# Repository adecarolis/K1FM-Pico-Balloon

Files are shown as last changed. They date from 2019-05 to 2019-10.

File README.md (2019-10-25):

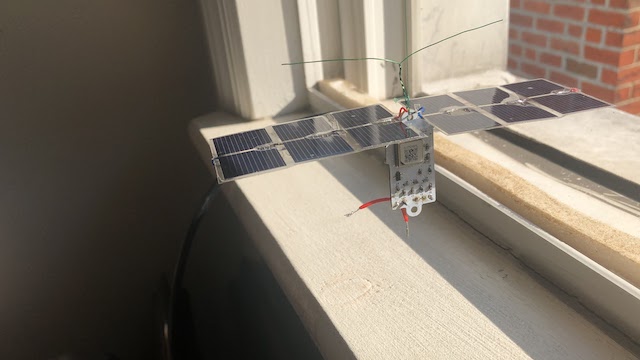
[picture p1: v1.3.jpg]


# K1FM Pico Balloon

## Introduction:

This tracker board is WSPR based and transmits on 20 meters. Version 1.3 weights 2.84 grams and takes around 55mA at 3.3V. Unlike other designs, this one includes a passband filter that significantly smooths the resulting waveforms (such filter would be legally mandatory in the United States). The board includes a power regulator and a low voltage dropout diode that can be useful if using batteries.

A maiden flight, powered by 6 39x19mm Aoshike solar panels, was attempted in New Jersey at the end of September 2019. After 5 days of transmissios the payload failed somewhere around Belize (central America) probably after encountering a tropical storm.

The recommended software is [GeminiWSPR](https://github.com/adecarolis/GeminiWspr)

Feel free to test these boards. You can purchase the latest revision (1.3) at OSHPark:

https://oshpark.com/shared_projects/ud3vH8MF

Suggestions and technical advice are welcome!

73 de Alain K1FM

## Assembly:

This is the recommended assemply sequence. Test each step individually. Do not proceed furter in case you enconter a problem in the current step.

- Install U1, C2, C3, C12, J2, Y1, R1, R2, R5 (Microcontroller)
- Use a USBasp programmer to load the Arduino bootloader (Atmel328p, 8MHz) via the ICSP port. Verify the bootloader can be uploaded without errors.
- Disconnect the USBasp from the J2 port. Connect a serial Arduino programmer to J3 (use 3V and GND connections from J2). Load the GeminiWSPR firmware (don't forget to set your own callsign and gridsquare!). Verify debug output can be seen on the serial monitor.
- Install GPS1, R6, Q2, C10 (GPS)
- Connect the GPS antenna
- In the Arduino serial monitor, verify the GPS is working
- Install Q1, U2, C11, C13, C14, R3, R4, R8, Q3 (Transmitter)
- Install L1, L2, L3, C5, C6, C7, C8, C9 (Bandpass filter)
- Connect the HF antenna 
- Verify the unit transmits WSPR on 14.0956 MHz
- Install U3, C1, C4, D1 (Power Supply)
Note: this is not needed if your power source is externally regulated or never exceeds 3.5 Volts
- Disconnect all J3/J2 connections. Verify the unit can be normally powered via J4

## Changelog:

**Version 1.0**
Initial, not functioning prototype.

**Version 1.1**
- Bugfixes

**Version 1.2**
- Added optional K1FM Pico Power board for battery charge management
- Added bottom hook for dipole antennas
- Replaced Si5351a quartz with TCXO (Q1)
- Added switches to power the Si5351a, GPS down (Q2 - Q3)
- Added temperature sensor (TMP-36)
- Added fixed V_BCK connection to 3.3V
- Added VDD measurement point (ADC0)

**Version 1.3**
- Switched to 4 Layers design
- Added Time Pulse feedback to external interrupt input (PD2)
- Added Clock Generator Feedback to T1 input (PD5)
- Added external SDA, SCL pins
- Added extra power pin for direct battery charging via Schottky diode
- Reorganized external pins, added standard ISCP header
- 4.7 voltage divider on ADC0
- Fixed Q2-Q3 Mosfet polarization
- Expanded gap between main board and "Remove Before Flight" section

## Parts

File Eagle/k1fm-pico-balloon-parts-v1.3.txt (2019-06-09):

Partlist

Exported from k1fm-pico-balloon-v1.3.brd at 6/9/19 8:12 AM

EAGLE Version 9.4.1 Copyright (c) 1988-2019 Autodesk, Inc.

Assembly variant: 

Part     Value                Package           Library               Position (mm)         Orientation

C1       1.0uF                0603              SparkFun-Capacitors   (6.510471875 54.445575) R90
C2       0.1uF                0603              SparkFun-Capacitors   (20.034125 62.95714375) R179.6
C3       0.1uF                0603              SparkFun-Capacitors   (0.527509375 77.5840375) R270
C4       1.0uF                0603              SparkFun-Capacitors   (13.97363125 54.226953125) R90
C5       56pF                 0603              SparkFun-Capacitors   (0.9513875 53.924478125) MR90
C6       18pF                 0603              SparkFun-Capacitors   (2.764634375 56.918090625) MR0
C7       47pF                 0603              SparkFun-Capacitors   (7.7810625 53.907934375) MR90
C8       18pF                 0603              SparkFun-Capacitors   (10.3251875 56.879790625) MR0
C9       56pF                 0603              SparkFun-Capacitors   (11.027996875 53.883903125) MR90
C10      0.47uF               0603              SparkFun-Capacitors   (1.418003125 65.57608125) MR90
C11      0.47uF               0603              SparkFun-Capacitors   (6.47683125 56.888134375) MR0
C12      1.0uF                0603              SparkFun-Capacitors   (22.828375 78.392015625) R180
C13      10nF                 0603              SparkFun-Capacitors   (13.004925 57.02285)  R180
C14      100nF                0603              SparkFun-Capacitors   (13.074546875 63.546453125) R180
D1       1A/23V/620mV         SOD-323           SparkFun-DiscreteSemi (8.938628125 50.169359375) R90
GPS-ANT  GPS ANT              1X02              SparkFun-Connectors   (8.6076125 77.45479375) R180
GPS1     UBLOX_MAX            UBLOX_MAX         Ava                   (8.54139375 69.8114625) MR270
HF-ANT   HF ANT               1X02              SparkFun-Connectors   (13.966375 50.042946875) R180
J1       I2C                  1X02              SparkFun-Connectors   (20.170153125 68.292134375) R270
J2       ICSP                 2X3               SparkFun-Connectors   (23.1168875 71.0920125) R90
J3       SERIAL               1X03              SparkFun-Connectors   (23.213425 63.25721875) R90
J4       POWER                1X03              SparkFun-Connectors   (1.074065625 50.128775) R0
L1       1.5uH                0603              SparkFun-Coils        (0.7136 60.571709375) MR270
L2       1.5uH                0603              SparkFun-Coils        (4.356440625 53.90499375) MR270
L3       1.5uH                0603              SparkFun-Coils        (13.370315625 55.87625) MR270
Q1       ASTX-H11-25.000MHZ-T 3.2X2.5_KXO-84    crystal-geyer_V1_0    (13.06335625 60.217428125) R270
Q2       DMP2305U             SOT23             transistor-fet        (13.089153125 77.525453125) MR90
Q3       DMP2305U             SOT23             transistor-fet        (13.0356375 60.57650625) MR90
R1       4.7k                 0603              SparkFun-Resistors    (0.56444375 54.44650625) R90
R2       10k                  0603              SparkFun-Resistors    (1.5009875 69.44980625) MR270
R3       4.7k                 0603              SparkFun-Resistors    (5.890165625 62.760128125) R270
R4       4.7k                 0603              SparkFun-Resistors    (9.07876875 62.5356875) R270
R5       1k                   0603              SparkFun-Resistors    (3.40955 54.446978125) R90
R6       1K                   0603              SparkFun-Resistors    (14.37328125 77.53238125) R90
R8       1K                   0603              SparkFun-Resistors    (4.545071875 60.513275) MR270
U1       ATMEGA328            TQFP32-08         SparkFun              (6.558065625 70.28035625) R180
U2       Si5351A-B-GT         MSOP10            microbuilder          (8.333103125 58.529059375) R90
U3       MCP1754X-XXXXX/C     SOT-23A_MC        MCP1754               (10.36651875 54.132665625) R90
U4       TMP36                SOT-23            TMP36                 (1.986578125 62.786390625) R180
Y1       8/16/20MHz           RESONATOR-SMD-1:1 Testing               (13.49439375 71.889096875) R90

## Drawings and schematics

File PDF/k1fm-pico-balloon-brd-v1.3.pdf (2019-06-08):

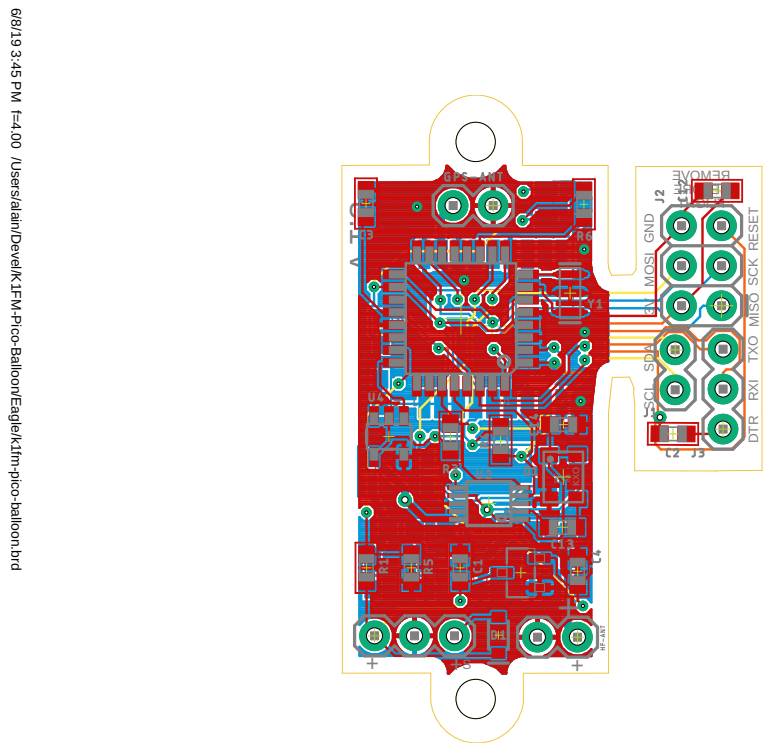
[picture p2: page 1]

6/8/19 3:45 PM f=4.00 /Users/alain/Devel/K1FM-Pico-Balloon/Eagle/k1fm-pico-balloon.brd

RXI TXO DTR SCK

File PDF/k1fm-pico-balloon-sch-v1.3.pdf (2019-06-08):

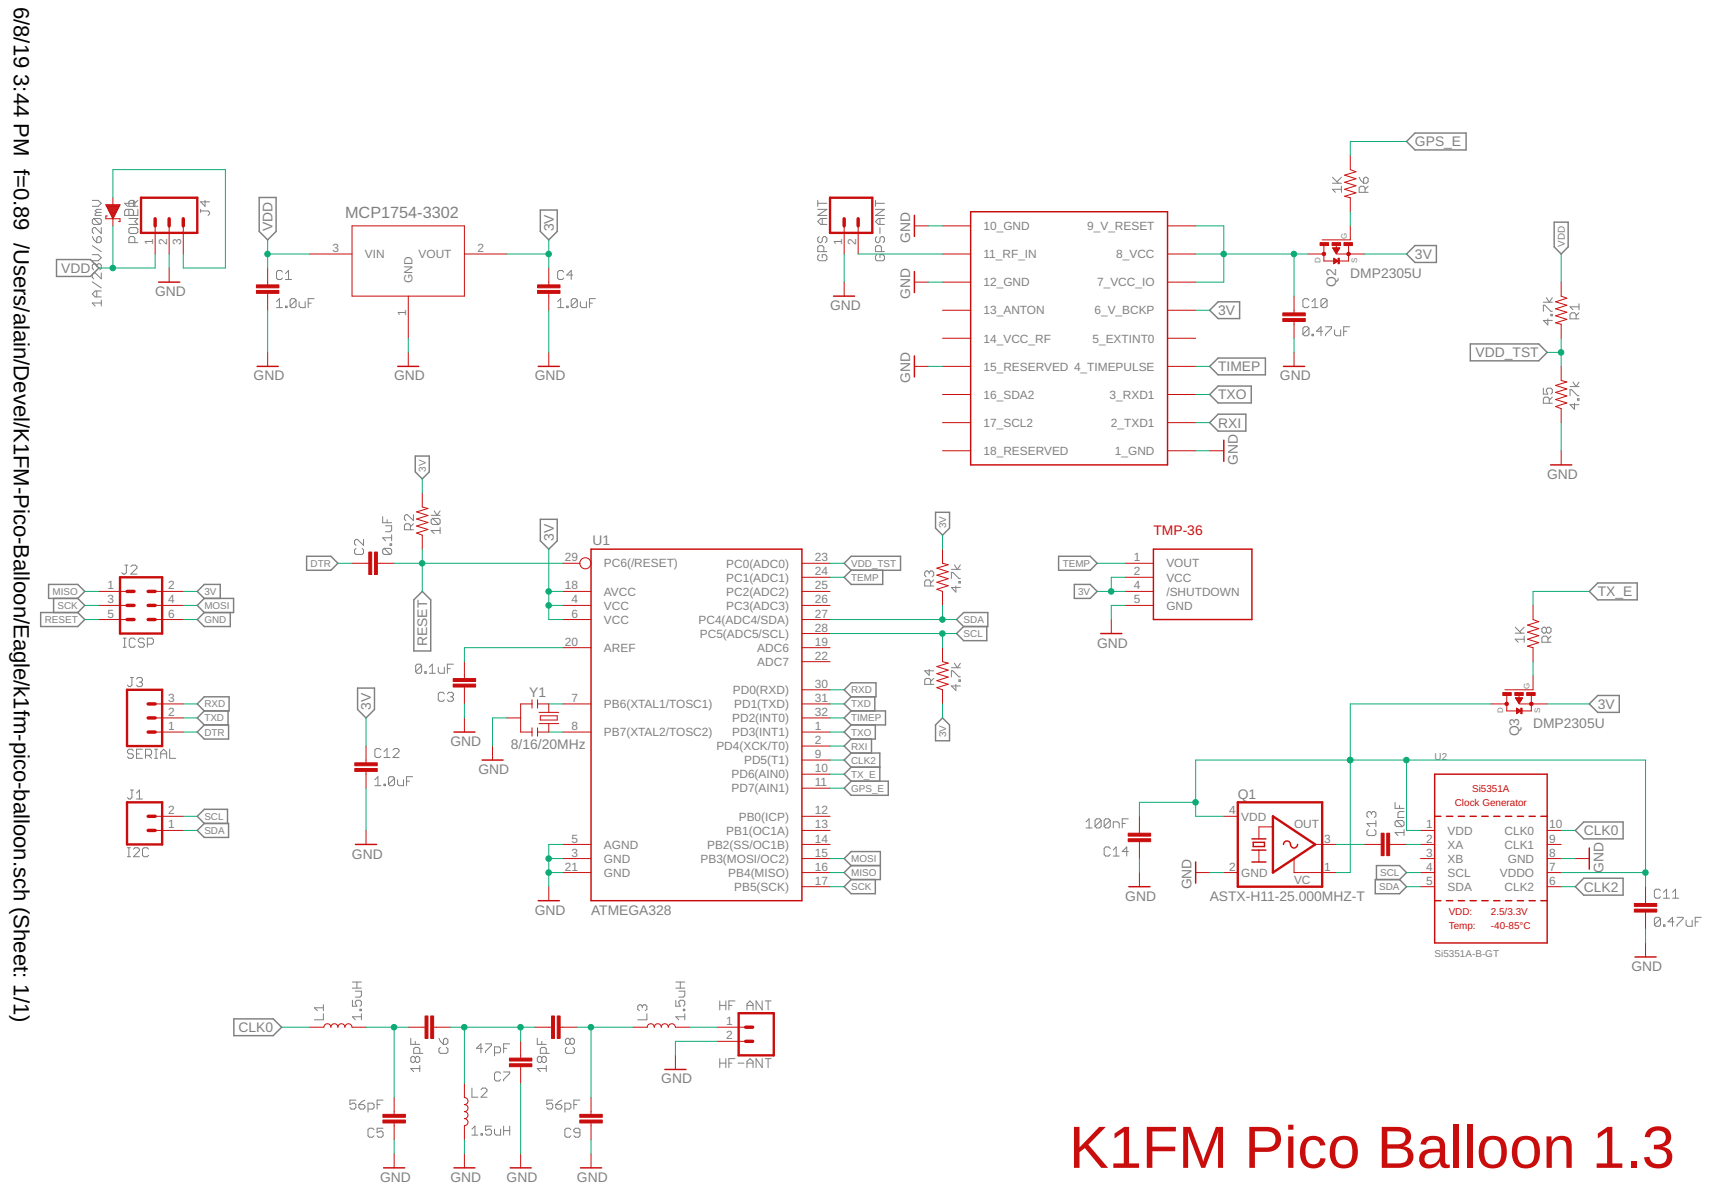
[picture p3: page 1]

6/8/19 3:44 PM f=0.89 /Users/alain/Devel/K1FM-Pico-Balloon/Eagle/k1fm-pico-balloon.sch (Sheet: 1/1)

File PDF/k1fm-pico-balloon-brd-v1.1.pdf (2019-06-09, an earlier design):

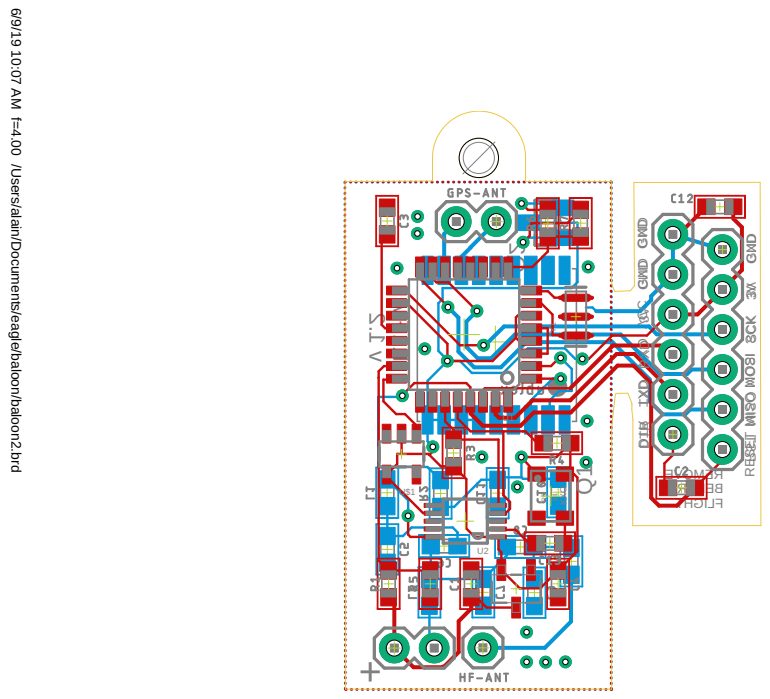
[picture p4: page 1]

6/9/19 10:07 AM f=4.00 /Users/alain/Documents/eagle/baloon/baloon2.brd

GND GND VCC RXD TXD DTR

GND 3V SCK MOSI MISO RST

SCK MOSI MISO RESET

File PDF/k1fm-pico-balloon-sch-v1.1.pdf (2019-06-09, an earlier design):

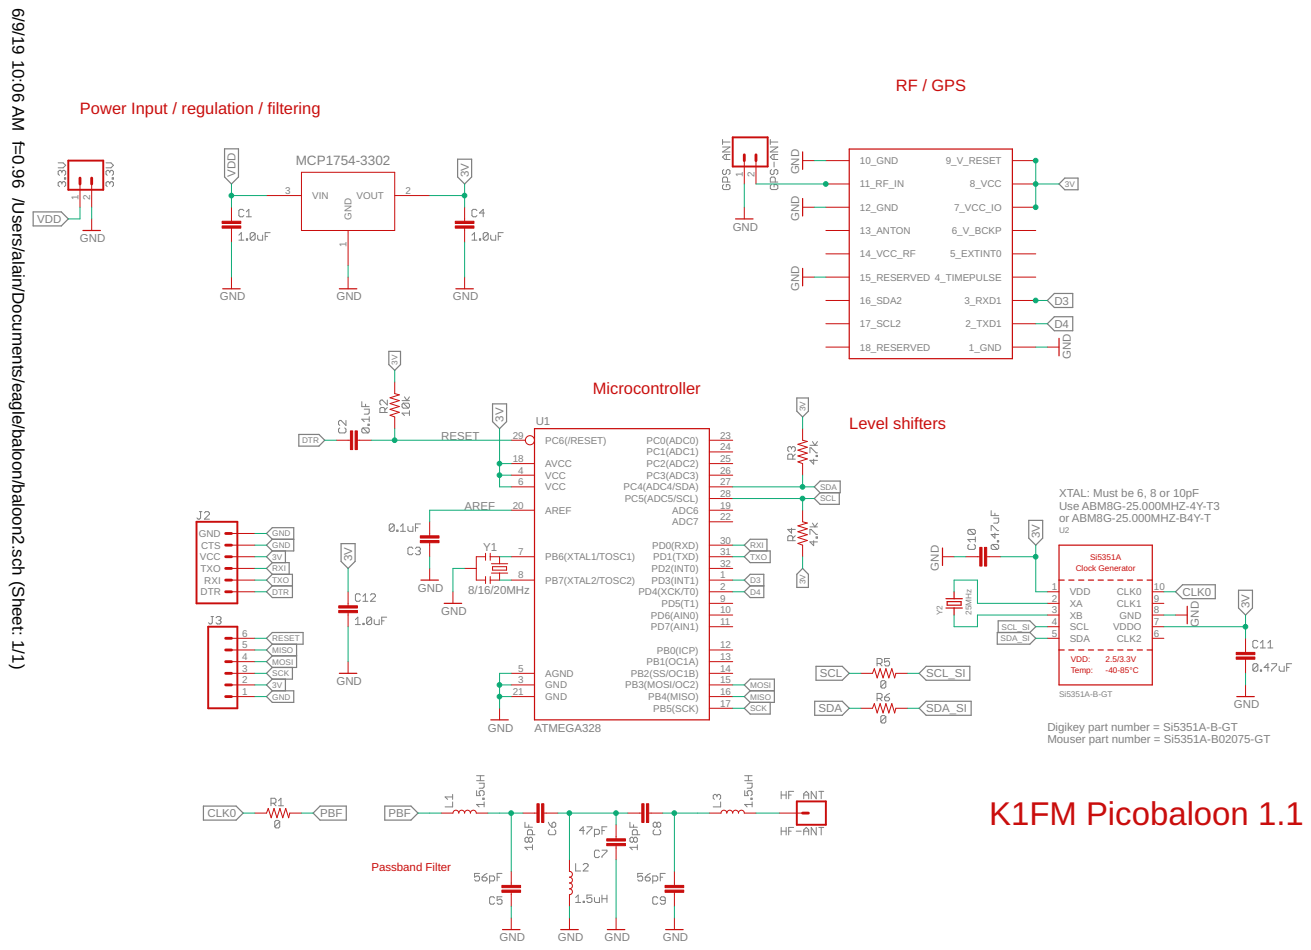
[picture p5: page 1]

6/9/19 10:06 AM f=0.96 /Users/alain/Documents/eagle/baloon/baloon2.sch (Sheet: 1/1) Digikey part number = Si5351A-B-GT Mouser part number = Si5351A-B02075-GT XTAL: Must be 6, 8 or 10pF Use ABM8G-25.000MHZ-4Y-T3 or ABM8G-25.000MHZ-B4Y-T GND GND GND GND GND GNDGND GND ATMEGA328 8/16/20MHz GND GND GND Si5351A-B-GT 25MHz GND GND GND GND GND GND MCP1754-3302 GND GND GND 10_GND 11_RF_IN 12_GND 13_ANTON 14_VCC_RF 15_RESERVED 16_SDA2 17_SCL2 18_RESERVED 9_V_RESET 8_VCC 7_VCC_IO 6_V_BCKP 5_EXTINT0 4_TIMEPULSE 3_RXD1 2_TXD1 1_GND PB5(SCK) 17 PB7(XTAL2/TOSC2) 8 PB6(XTAL1/TOSC1) 7 GND 3 GND 21 VCC 4 VCC 6 AGND 5 AREF 20 AVCC 18 PB4(MISO) 16 PB3(MOSI/OC2) 15 PB2(SS/OC1B) 14 PB1(OC1A) 13 PB0(ICP) 12 PD7(AIN1) 11 PD6(AIN0) 10 PD5(T1) 9 PD4(XCK/T0) 2 PD3(INT1) 1 PD2(INT0) 32 PD1(TXD) 31 PD0(RXD) 30 ADC7 22 ADC6 19 PC5(ADC5/SCL) 28 PC4(ADC4/SDA) 27 PC3(ADC3) 26 PC2(ADC2) 25 PC1(ADC1) 24 PC0(ADC0) 23 PC6(/RESET) 29 U1 Y1 VDD 1 XA 2 XB 3 SCL 4 SDA 5 CLK2 6 VDDO 7 GND 8 CLK1 9 CLK0 10 U2 Y2 DTR RXI TXO VCC CTS GND 12 123456 12 GND 1 VOUT 2 VIN 3 GND GND GND D3 D3 D4 D43V 3V 3V 3V 3V 3V 3V 3V 3V 3V 3V MISO MISO MOSI MOSI SCK SCK AREF RESET RESET DTR DTR TXO TXO RXI RXI SDA SDA SCL SCL CLK0 CLK0 PBF PBF SCL_SI SCL_SI SDA_SI SDA_SI VDD VDD K1FM Picobaloon 1.1 Power Input / regulation / filtering RF / GPS Microcontroller Level shifters Passband Filter Si5351A Clock Generator VDD: 2.5/3.3V Temp: -40-85°C

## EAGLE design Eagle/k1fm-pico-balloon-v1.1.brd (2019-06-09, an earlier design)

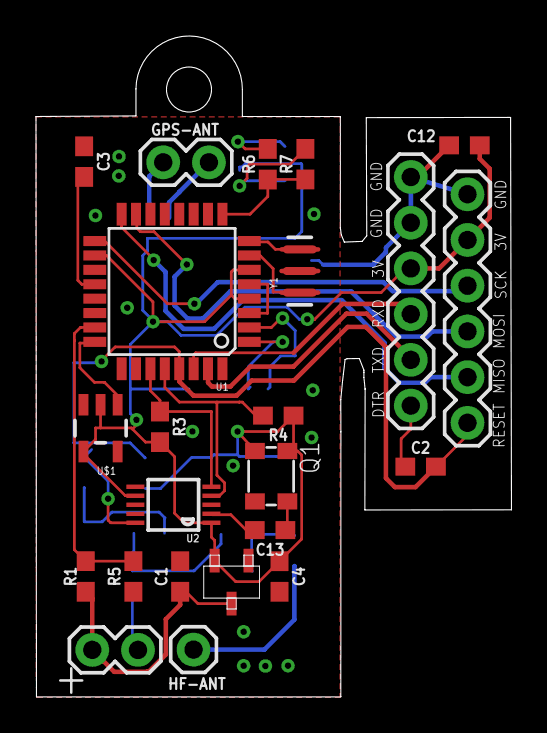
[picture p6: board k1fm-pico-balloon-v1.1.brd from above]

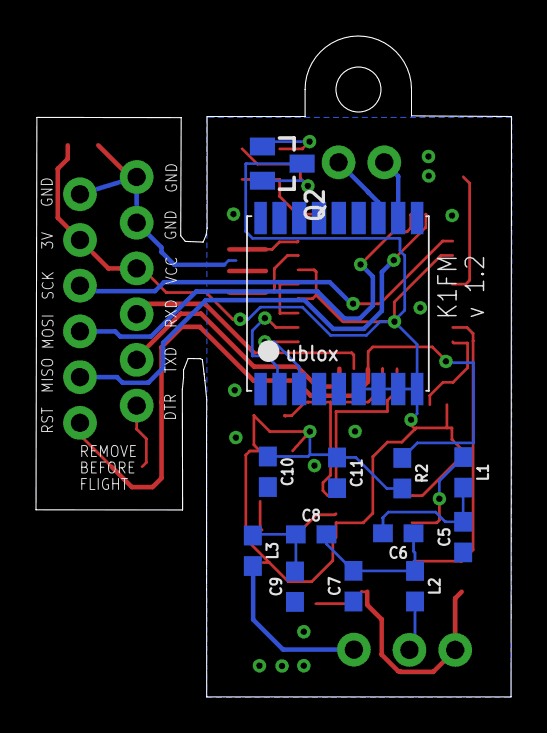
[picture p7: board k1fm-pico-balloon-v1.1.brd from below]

Board: 2 copper layers, 26.4 x 36.7 mm, 36 parts (13 on the bottom side), 30 nets.

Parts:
3.3V: 3.3V; 1X02
C1, C4, C12: 1.0uF; 0603
C2, C3: 0.1uF; 0603
C5, C9: 56pF; 0603
C6, C8: 18pF; 0603
C7: 47pF; 0603
C10, C11: 0.47uF; 0603
C13: 10nF; 0603
GPS1: UBLOX_MAX
GPS-ANT: GPS ANT; 1X02
HF-ANT: HF ANT; 1X01
J2, J3: 1X06
L1, L2, L3: 1.5uH; 0603
Q1: ASTX-H11-25.000MHZ-T; 3.2X2.5_KXO-84
Q2: DMP2305U; SOT23
R1, R2, R5, R7: 10k; 0603
R3, R4: 4.7k; 0603
R6: 150; 0603
U1: ATMEGA328; TQFP32-08
U2: Si5351A-B-GT; MSOP10
U3: MCP1754X-XXXXX/C; SOT-23A_MC
U$1: TMP36; SOT-23
Y1: 8/16/20MHz; RESONATOR-SMD-1:1

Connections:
3V: C4.1, C10.1, C11.1, C12.1, GPS1.6_V_BCKP, GPS1.7_VCC_IO, GPS1.8_VCC, GPS1.9_V_RESET, J2.4, J3.2, Q1.1, Q1.4, Q2.3, R2.2, R3.2, R4.1, U1.4, U1.6, U1.18, U2.1, U2.7, U3.2, U$1.2, U$1.4
ANT: HF-ANT.1, L3.2
AREF: C3.2, U1.20
CLK0: L1.1, U2.10
D3: GPS1.3_RXD1, U1.1
D4: GPS1.2_TXD1, U1.2
DTR: C2.1, J2.1
GND: 3.3V.2, C1.2, C3.1, C4.2, C5.1, C7.1, C9.1, C10.2, C11.2, C12.2, GPS1.1_GND, GPS1.10_GND, GPS1.12_GND, GPS1.15_RESERVED, GPS-ANT.1, J2.5, J2.6, J3.1, L2.2, Q1.2, R5.1, U1.3, U1.5, U1.21, U2.8, U3.1, U$1.5, Y1.2
GPS_E: R6.1, R7.1, U1.9
MISO: J3.5, U1.16
MOSI: J3.4, U1.15
unnamed: C13.1, Q1.3
unnamed: C13.2, U2.2
unnamed: Q2.2, R7.2
unnamed: R1.2, R5.2, U1.23
unnamed: Q2.1, R6.2
unnamed: GPS1.11_RF_IN, GPS-ANT.2
unnamed: C6.1, C7.2, C8.2, L2.1
unnamed: C5.2, C6.2, L1.2
unnamed: C8.1, C9.2, L3.1
unnamed: U1.8, Y1.3
unnamed: U1.7, Y1.1
RESET: C2.2, J3.6, R2.1, U1.29
RXI: J2.3, U1.30
SCK: J3.3, U1.17
SCL: R4.2, U1.28, U2.4
SDA: R3.1, U1.27, U2.5
TEMP: U1.24, U$1.1
TXO: J2.2, U1.31
VDD: 3.3V.1, C1.1, R1.1, U3.3

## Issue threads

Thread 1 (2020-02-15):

In rush current on GPS and Si5351 trips CPU under voltage

TimMW1, 2020-02-15:
While using the latest version of Orion with the turn on FETs enabled, the CPU gets into a reset loop due to a drop on the 3v rail when the GPS and Si PLL get enabled.  A soft start cap on the FET gate an/or more Bulk would fix this issue.

mrpatrick1991, 2020-10-03:
Can confirm a reboot loop on start with V1.3 of the board running either the GeminiWSPR or OrionWSPR software.

Attempted to correct this by adding 300uF capacitors on the 3v rail as well as soft-start on the mosfet gates. The behavior was not changed.

Running simple test programs on the si5351 and gps allow me to turn on and use both simultaneously without issue, so I suspect it is a software problem (?)

Any insight would be appreciated.

adecarolis, 2020-10-03:
Hello Tim and Patrick. Sorry for the inconvenience.
I apologize for replying so late but I never noticed this issue until Patrick sent me a direct email (thanks for that).

I am not familiar with any reboots but I will try to assemble another board ASAP and try to reproduce the issue.
Meanwhile, since you clearly have a problem, please just bypass those FETs, like so: https://imgur.com/a/XCQ49I2
In this configuration, the board must work as it flew successfully at least 3 times.

The only issue I had related to those FETs was software related. I remember that during flight, if I unpowered the si5351 and/or the GPS I would not always be able to restart them in a functional state unless I rebooted the micro, which was unfortunate and inconvenient. I attributed the issue to I2C (apparently you can't simply power off a connected I2C device and then simply power it back on). For this reason, in GeminWspr I immediately power on both devices and leave them powered all along. The good news is that in the current configuration there is more than enough current to have all the components powered at all times, so bypassing the FETs isn't a problem. I normally don't even install them anymore.

The reason why I introduced them was because they were requested by other users of the board. I also was planning to leverage them in a subsequent release that uses a step-up regulator capable of powering the whole thing on a single panel. For now, you don't need them, so feel free to bypass them altogether. In any case, I will assemble a new board ASAP and try to reproduce the issue you describe. I will post updates here.

Thanks again!

mrpatrick1991, 2020-10-05:
Hey - thanks for the reply! I'll report back after trying to bypass the MOSFET's.

mrpatrick1991, 2020-10-09:
Bypassing the MOSFET's does not appear to change the reset behavior. This is with a bench 3.3v supply connected to the 3.3v rail, and the OrionWSPR V1.0 software with the K1FM board definition.

Does anyone have any other ideas?

adecarolis, 2020-10-18:
Hello,

I was 100% sure in the first place that there isn't an overcurrent issue but in order to triple check I just finished assembling another board. **No issues were found: TX is OK, GPS is OK, drawn current never exceeds 50mA at 3.3V**.

Your issues might or might not be related. When there is a short or any other soldering defect more often than not you end up with issues similar to the one you describe. This is precisely why I recommend an incremental assembly procedure: you might want to catch an eventual issue early on rather than at the end of the build.
To troubleshoot, I suggest removing components applying the procedure in reverse order until you reach a point where the overcurrent doesn't happen anymore. At that point you will know where the problem is.

I'm closing the issue. Good luck!

Closed 2020-10-18.

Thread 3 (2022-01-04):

Just a typo....

frohro, 2022-01-04:
Hi Alain,
Thanks for sharing your design.

i just noted a typo, and thought I'd try to do a little to help you, after all you have done for me.  In the README, you have
"Do not proceed furter in case you".  I think you wanted further.  :-)
I note ZachTek puts a 10K resistor across the HF dipole, and I'm guessing it might be to help dissipate static electricity.  I also note that [KD9ORR](http://lu7aa.com.ar/wspr.asp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) is using a [fishing swivel ](https://nibbborg.files.wordpress.com/2021/12/how-to-tie-a-knot.jpg?w=480)which may relieve some strain on their HF antenna.  I am wondering if the larger solar panels you were using and their larger wind load made it harder for your balloon to survive, along with multiple balloons which seem more likely to spin in the wind causing metal fatigue in your wires.  For this reason, I'm wondering if a bigger capacitor and smaller solar panels might be better.  What do you think?

I'm curious why you used a bandpass filter instead of a low pass filter on your HF output?

Do you have any new thoughts?  As one of the experiments we are planning, I'm working on modifying your design so it uses parts that are available from JlCPCB.  Building things is getting harder due to parts shortages these days.

Again, thanks for sharing!

73,

Rob
KL7NA

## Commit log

2019-05-15 Add Eagle schmatics and boards
    [k1fm-pico-balloon.brd, k1fm-pico-balloon.sch, k1fm-pico-power.brd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]
2019-05-25 4 Layers. Added external SCL, SDA, GPS lines.
    [k1fm-pico-balloon.brd, k1fm-pico-balloon.sch]
2019-05-25 Reorganized TX/RX lines - Conn layout
    [k1fm-pico-balloon.brd, k1fm-pico-balloon.sch]
2019-05-25 Add diode and connection for direct solar power
    [k1fm-pico-balloon.brd, k1fm-pico-balloon.sch]
2019-05-25 Move board label
    [k1fm-pico-balloon.brd]
2019-05-26 Revert to classic hw/sw serial configuration
    [k1fm-pico-balloon.brd, k1fm-pico-balloon.sch]
2019-05-26 Redraw VDD measure input
    [k1fm-pico-balloon.brd, k1fm-pico-balloon.sch]
2019-05-27 Use diode BAT20J, space out break lines, bugfix
    [k1fm-pico-balloon.brd, k1fm-pico-balloon.sch]
2019-05-29 Use PD2 (ext int) and PD5 (T1) for calibration
    [k1fm-pico-balloon.brd, k1fm-pico-balloon.sch]
2019-06-08 Fix Mosfet polarization
    [k1fm-pico-balloon.brd, k1fm-pico-balloon.sch]
2019-06-08 Expand gap
    [k1fm-pico-balloon.brd]
2019-06-09 Fixed R1-R5 voltage divider, fixed PCB warnings
    [k1fm-pico-balloon.brd, k1fm-pico-balloon.sch]
2019-06-09 Move Pico Power to separate directory
    [k1fm-pico-power.brd, k1fm-pico-power.sch]
2019-06-09 Move k1fm-pico-balloon.sch
    [k1fm-pico-balloon-v1.2.brd, k1fm-pico-balloon-v1.2.sch]
2019-06-09 Fix schematic name
2019-06-09 Rename files
    [k1fm-pico-balloon-v1.3.brd, k1fm-pico-balloon-v1.3.sch]
2019-06-09 Remove wire stubs
    [k1fm-pico-balloon-v1.3.brd]
2019-06-09 Add v1.1, fix PDFs
    [k1fm-pico-balloon-v1.1.brd, k1fm-pico-balloon-v1.1.sch]
2019-06-09 Add v1.0
    [k1fm-pico-balloon-v1.0.sch]
2019-09-28 Remove pico power
    [k1fm-pico-power.brd, k1fm-pico-power.sch]
2019-09-28 Remove pico power PDF

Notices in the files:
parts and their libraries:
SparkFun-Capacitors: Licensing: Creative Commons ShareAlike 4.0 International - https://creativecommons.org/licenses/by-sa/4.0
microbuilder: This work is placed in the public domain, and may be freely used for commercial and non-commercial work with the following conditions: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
